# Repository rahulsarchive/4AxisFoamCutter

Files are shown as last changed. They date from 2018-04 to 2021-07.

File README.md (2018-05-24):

# 4AxisFoamCutter

Our goal was to build an UAV out of foam, since there will be many crashes involved, we decided to make a device to help us get through the iterations a bit faster. A hot wire cutter is the most efficient way to cut foam. A CNC hot wire cutter is even better! It is an awesome tool to have when you are building airplanes out of foam. A properlly configured machine can save you a lot of time and produce a smooth cut.

Mechanically, its not complicated to make a CNC Hot wire cutter. All you need is 4 independed linear axes, two horizontal axes and two vertical axes stacked on top of it. This can be acheived by any means such as linear bearings, smooth rods and also drawer slides. The axes are driven by stepper motors. There are minimal cutting forces involved, the machine only needs to be rigid enough to witstand the tension of the wire streched between the towers.

The problem is how to control 4 independent axes at the same time. Most tutorials online are for 3-axis 3D printers. Then there are documentation on people using expensive software and difficult to find hardware for making their 4-axis foam cutter.There does not seem to be enough documentation on building a 4-axis machine using easily available parts such as parts from a 3D printer kit and open source sotware. We found some people who had done similar projects using Arduino and Grbl, and decided to make a CNC hot wire cutter ourselves and try it out.

## Hot wire CNC Resources

[Hot wire cutter, RcKeith](http://www.rckeith.co.uk/cnc-hot-wire-foam-cutter/)  
[4-axis cnc hotwire cutter (arduino+Ramps)](https://www.rcgroups.com/forums/showthread.php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)  
[WingGcode](https://github.com/swarfer/winggcode)  
[Airfoil coordinates database](http://m-selig.ae.illinois.edu/ads/coord_database.html)  
[Free CNC Software](http://www.rckeith.co.uk/free-cnc-software-3-and-4-axis/)  
[4-axis Arduino based Hot wire cutter](https://www.rcgroups.com/forums/showthread.php?2388809-4-axis-Arduino-based-CNC-hot-wire-foam-cutter)  
[Devcnc Foam cutting software](http://www.devcad.com/eng/devcncfoam_f1_3.asp)  
[Jedicut foam cutting software](https://www.jedicut.com/)  
[Arduino Uno based foam cutter](https://sites.google.com/site/foamcuttercnc/software)  
[Nichrome wire Application Calculator](http://www.jacobs-online.biz/nichrome/NichromeCalc.html)  
[G-codes simply explained](https://all3dp.com/g-code-tutorial-3d-printer-gcode-commands/)

## Hardware

1. Plywood (12mm)
2. Rails (Steel tubes, Smooth rods)
3. Stepper Motors (one for each axis)
4. Lead screw (M8 x 600mm, as long as you need the axis to be)
5. Ramps 1.4
6. A4988 Stepper driver (one for each axis)
7. Arduino Mega 2560
8. Nichrome wire (30 guage for smaller builds and 26 guage for larger ones)
9. M8-M5 Motor coupler (M8 for the thread and M5 for the motor shaft)

## Software

1. Grbl Hotwire Controller   
2. 4-Axis G-code Generator  
    1. Wing Gcode  
    2. Jedicut  
    3. FoamXL  
 
We realized that the most difficult part of making a CNC hot wire cutter was the G-code and Controlling systems. So we decided to start from there. In our inital research we found many people using DevFoam and profilli for generating the G-code and using Mach3 to control their machine. But unfortunately, these softwares were not free and to run a Mach3 machine you need a parallel port, which is outdated now. Then our search lead to an Arduino based 4-axis cutter developed by [Marginally clever](https://www.marginallyclever.com/) which used an arduino Mega2560 and the Ramps 1.4 CNC sheild.

His page has codes for moving 4 independent axis and a Java based [G-code sender](https://github.com/MarginallyClever/GcodeSender) application that could send the the G-code secquentially to the Arduino using the serial port. We tried this solution and after some fiddiling around, we got it working. Not the easiest or most straight forward method. There is almost not documentation on how to use it.

[RcKeith](http://www.rckeith.co.uk/cnc-hot-wire-foam-cutter/) has some good documentation on the machines he built and what he used to control them. Some of them use expensive software and outdate hardware, which might be difficult to find.

We finally stumbled on a solution that worked, it was posted on a forum in rcgroups.com. Its for a [4 axis foam cutter using Arduino + Ramps1.4](https://www.rcgroups.com/forums/showthread.php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) It addressed the major problems we were having like a control software for the machine and generating 4-axis Gcode to drive the machine.

## Building the Machine

My intial design was based on Rckeith's foam cutter which used drawer slides as the linear guideways. This seemed like a good idea. They were locally available and rails are rigid without much backlash. The first design was for a machine with two towers on linear slides, with a total travel of the towers for about 20 inches. The machine would be laser cut out of 4mm plywood.

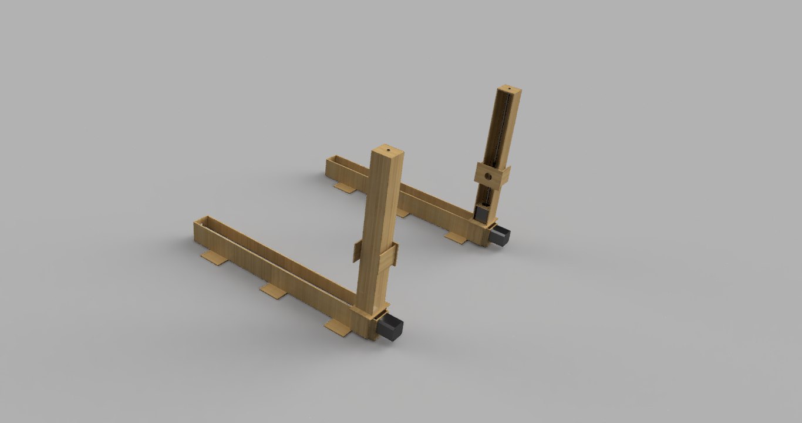
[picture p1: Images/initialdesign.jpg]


This was well and good, until we went to the shop to buy the slides. A 20 inch drawer slide can only travel 10 inches, so inorder to get 20 inches of travel we would need a slide of 40 inches, which were just too bulky and expensive for our use and the rails would protrude out of the machine for about 20 inches. Hence we dropped the plans for using drawer slides. Back to the drawing board.

We started on a new design for a more rigid maachine using smooth rods and leadscrews for motion.

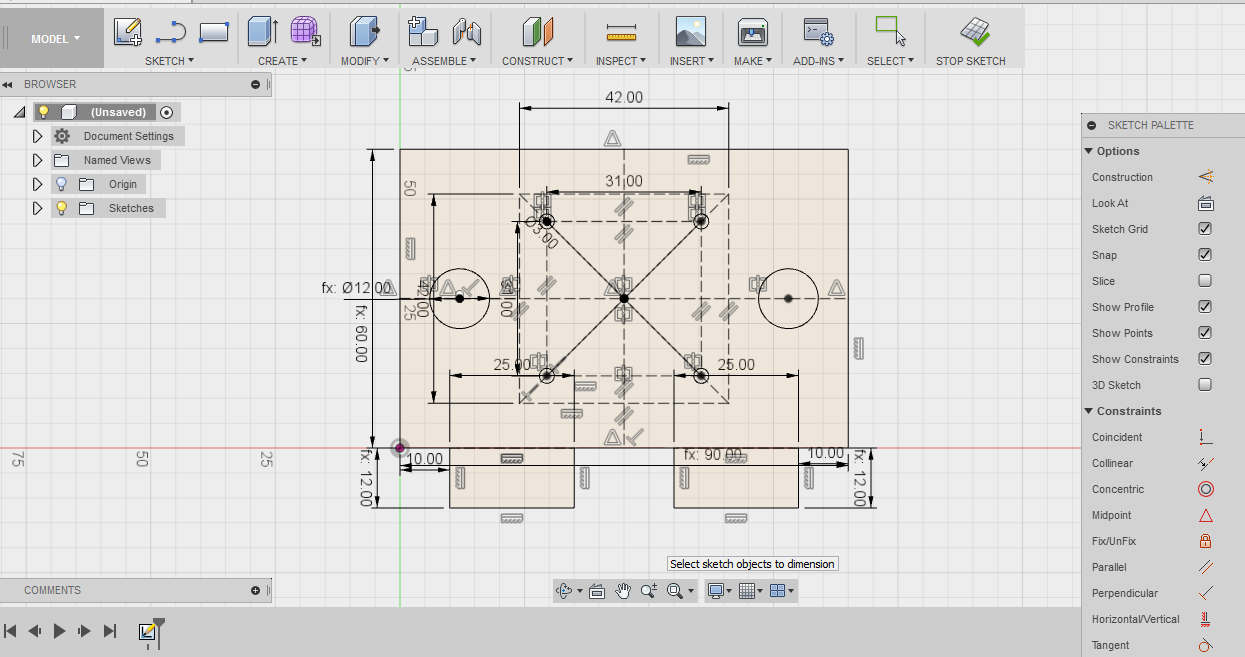
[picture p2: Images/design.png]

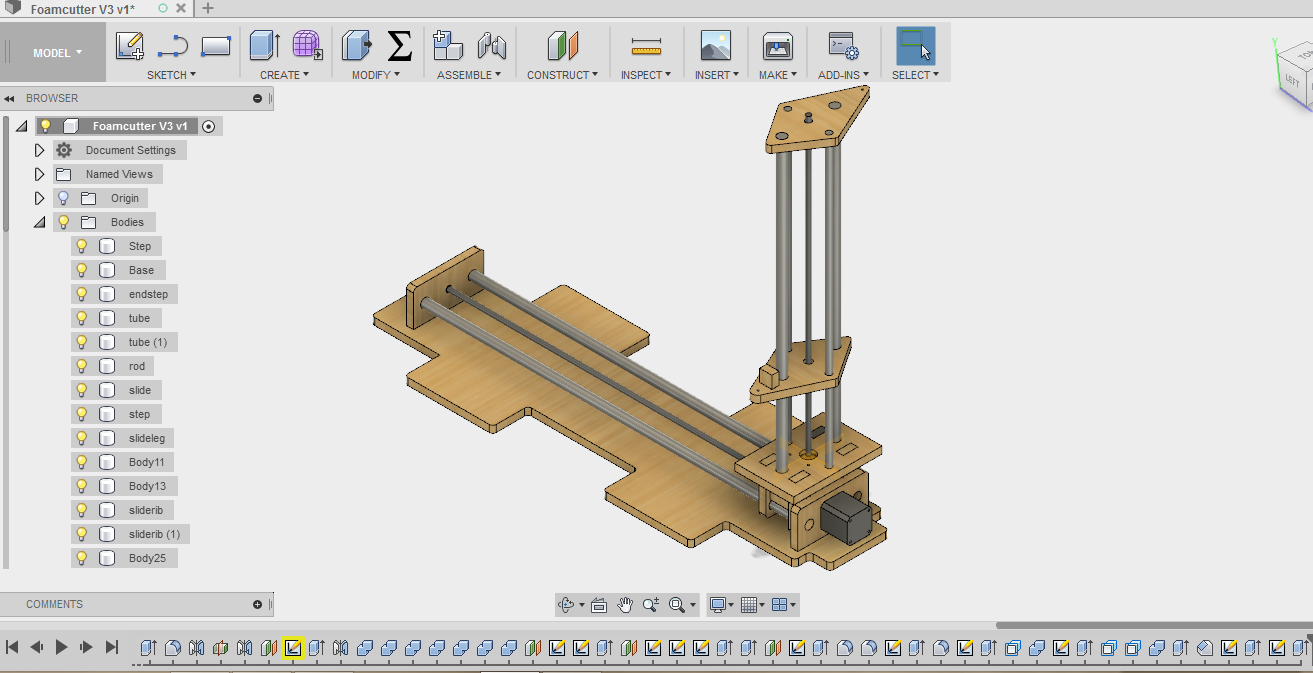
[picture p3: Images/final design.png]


The design is fully parametric. You can change the length of each axes, the diamter of the rods and even the clearance height of the vertical axis by changing the parameters in the file. On the vertical axes there are 4 rods to provide some torsional rigidity so the towers would not bend.

This is the fully redesigned machine using 1/2 inch steel tubes, 12 mm plywood as the base and M8 lead screws to move the axes. 

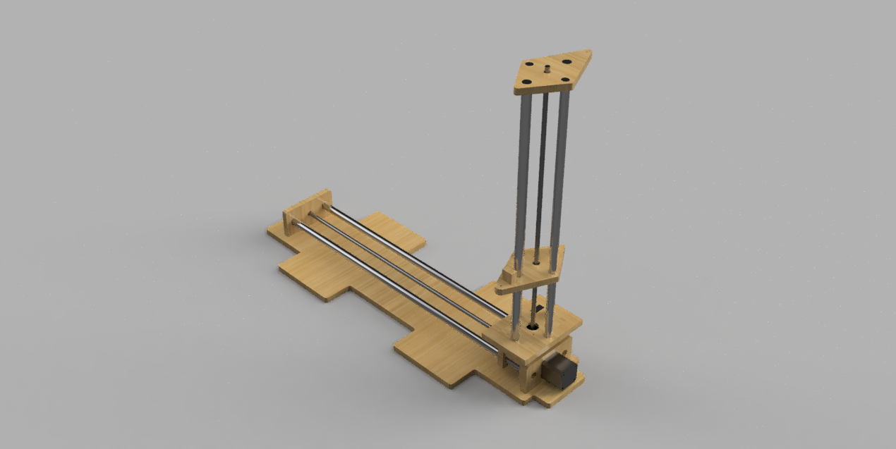
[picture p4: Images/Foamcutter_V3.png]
4 axis foam cutter


All the parts, except the lead screws were bought locally. The half inch steel tubes were not designed for linear bearings and there are not dimensionally accurate. So our plan was to 3D print a coupling for it to reduce the friction between wood and the steel.

The design made ready for milling on Shopbot (CNC mill) 

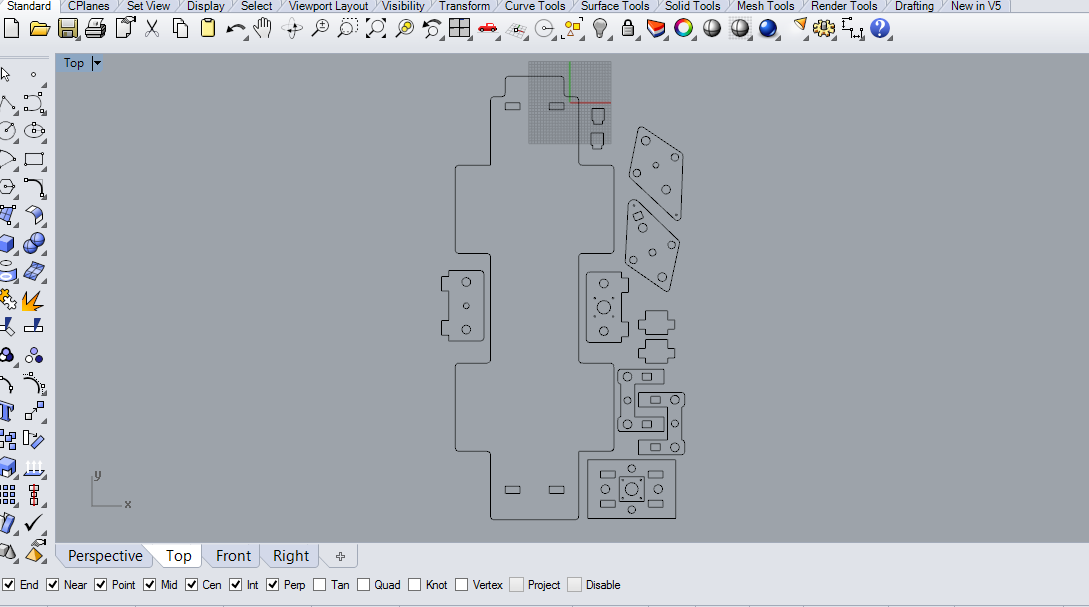
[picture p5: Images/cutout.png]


We cut the design by exporting the 2D DXF sketches and doing the CAM operations in Vcarvepro software. Since this is the intial version we decided to skip the couplers and go with wood on steel. we had to play with the tolerance between the circular hole and the steel tube to get it good enough to move on to the next step.

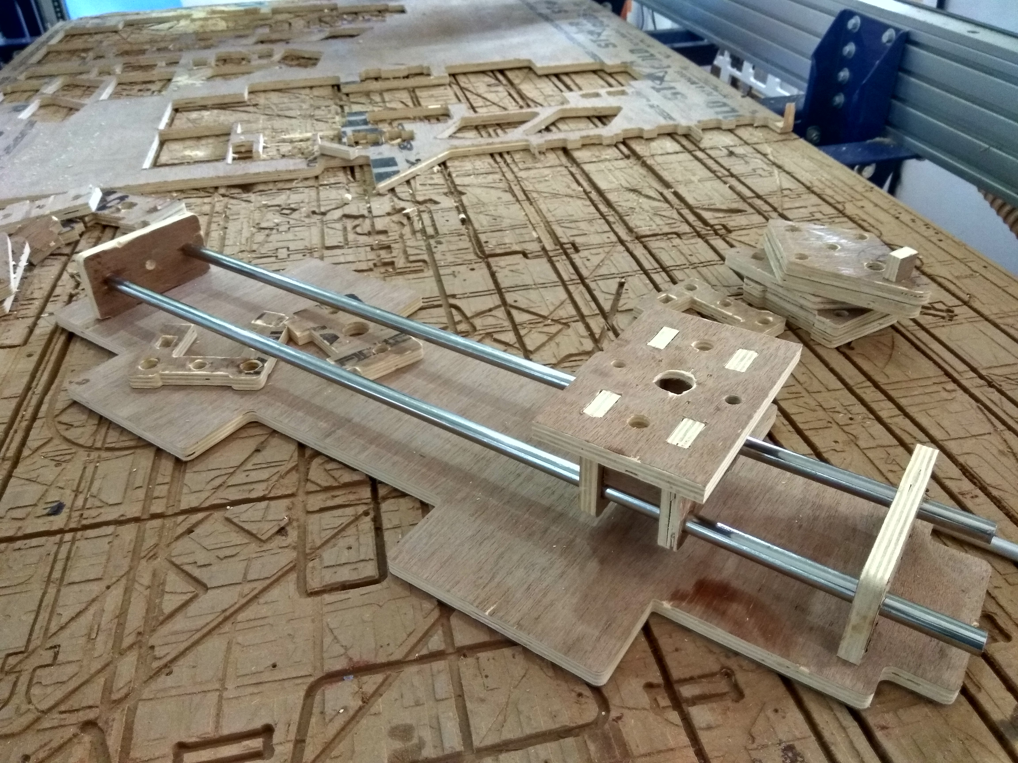
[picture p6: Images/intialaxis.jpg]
4 axis foam cutter


The first axis looks promising. The steel tubes are press fitted at the ends to form a rigid strucutre. The carriage is a bit loose but the motion is a lot smoother when a small amount of lubricant is applied. so we moved on to the vertical axis.

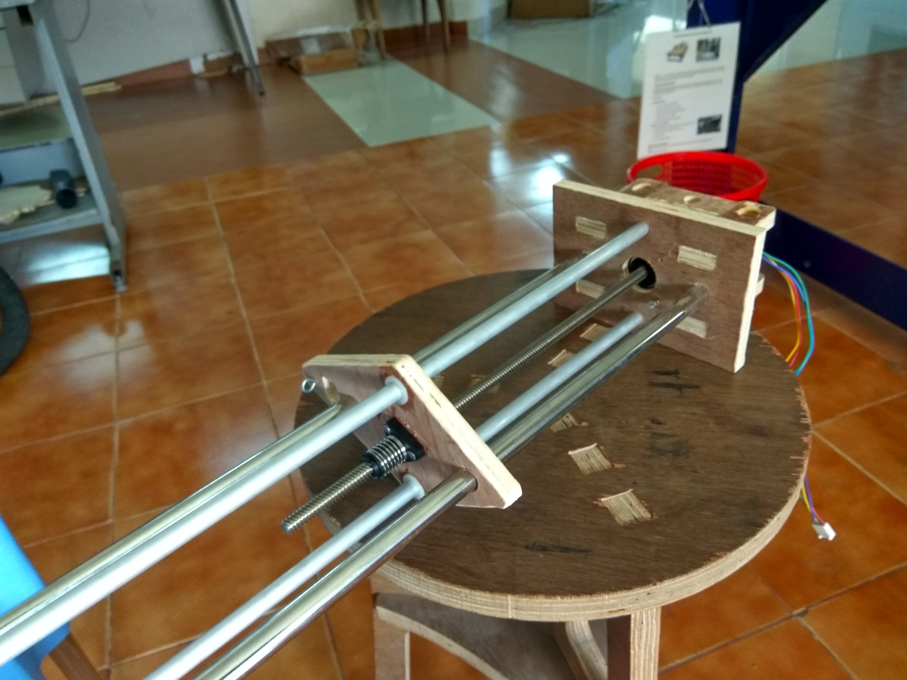
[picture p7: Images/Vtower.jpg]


The vertical axis has two steel tubes to carry the weight and two smaller aluminum tubes to provide tortional rigidity. We are using a stepper motor with an integrated lead screw to avoid using a coupler. 

The final assembled towers. All the rods are press-fit at the ends and loose fit on the steel rods to give a smoooth motion.

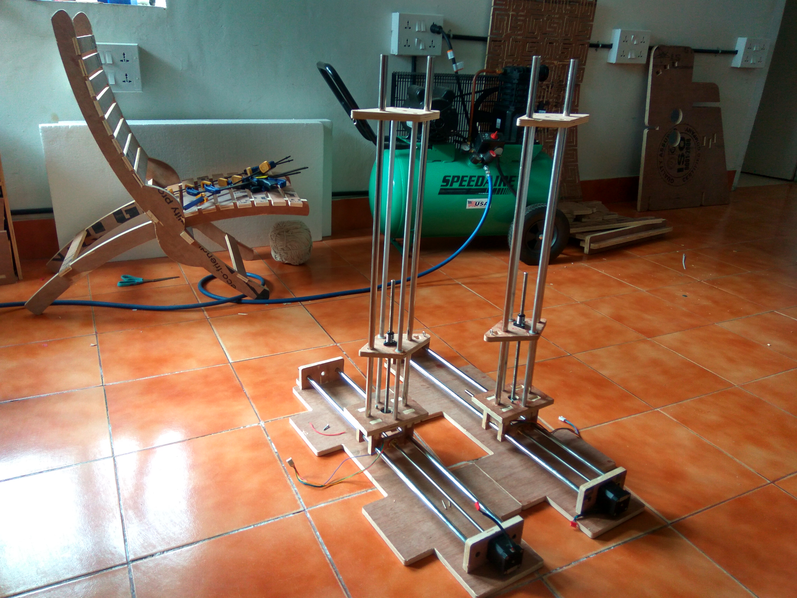
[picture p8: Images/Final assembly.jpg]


**Note-** When using sliding surfaces, depending on the material, a phenomenon called **'stick and slip'** can happen. This would cause the motion to become jagged and cause vibrations. It may also lead to surfaces locking up leading to excessive loads and missed steps when using a stepper motor.  

After the machine was assembled its time for fix the machine on a table, connect all the electronics and tie the Nichrome wire across the towers.

### Connecting the Electronics

We fixed the machine on a table using clamps. The base is designed to make it easier to use clamps to hold it in place. 

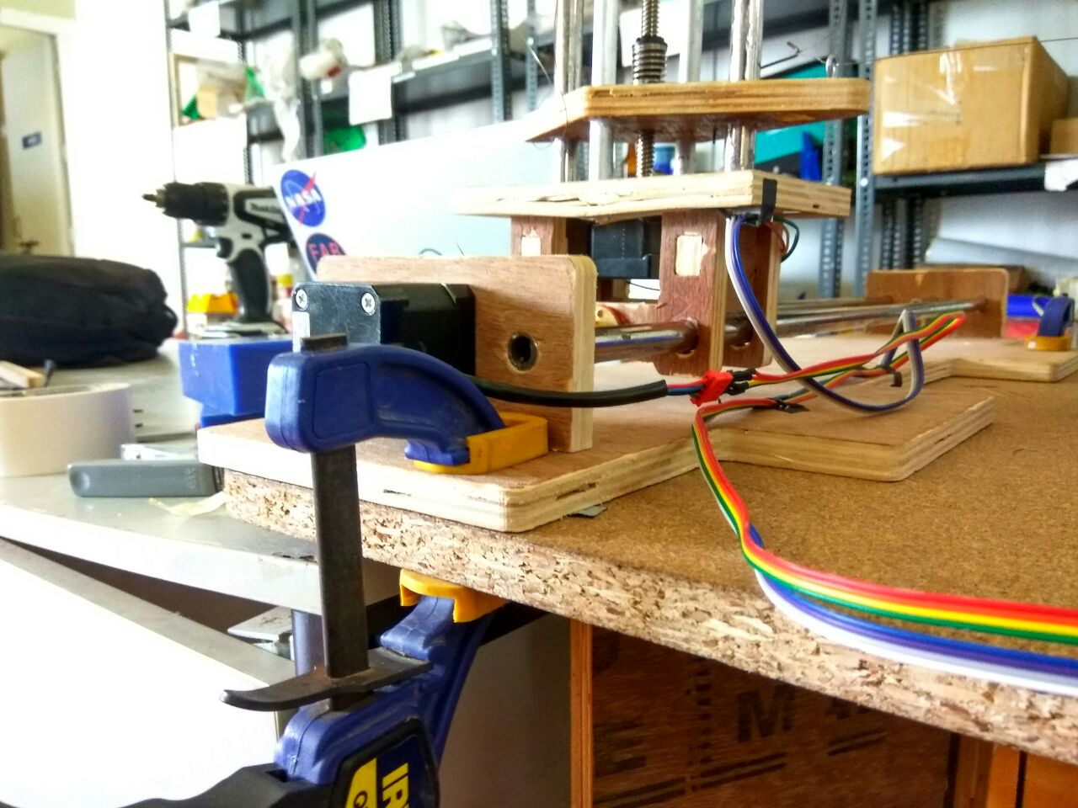
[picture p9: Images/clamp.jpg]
4 axis foam cutter assembly


The next step is to connect the electronics to move the motors and configure the machine. We have 4 stepper motors which need to be connected to our Ramps board. The wires need to extend enough to provide enough travel of the axes.

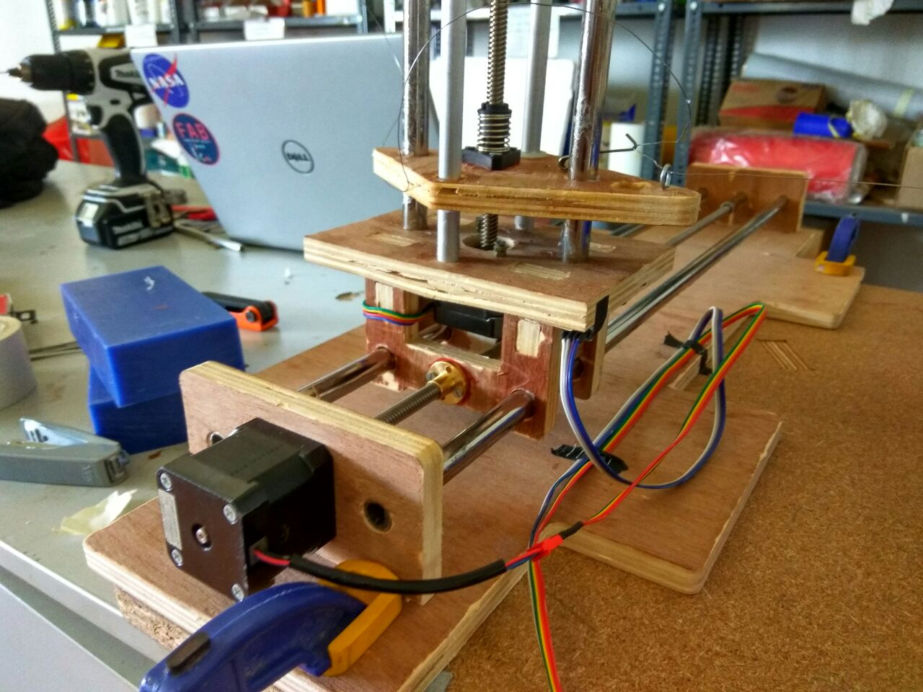
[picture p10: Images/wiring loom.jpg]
Wiring loom


All the wiring connects to our Ramps board, which is a CNC sheild for Arduino Mega2560. The Ramps can support upto 5 stepper motor drivers like the A4988. We are using Nema 17 motors with 200 steps per revolution running at 1/16th microstepping, giving us a smooth rotary motion.

The A4988 stepper drivers can be attached on top of the Ramps, one for each axis. Ensure **proper orientation** of the A4988 chip before attaching to the Ramps board. Each stepper can pull as much as 2 Amps, the stepper drivers have heat sinks to dissipate the heat. The board also has a 11A MOSFET on it to control the temperature of the wire connected to the D8 pin. All the components in the board will get hot, ensure proper cooling is provided. 

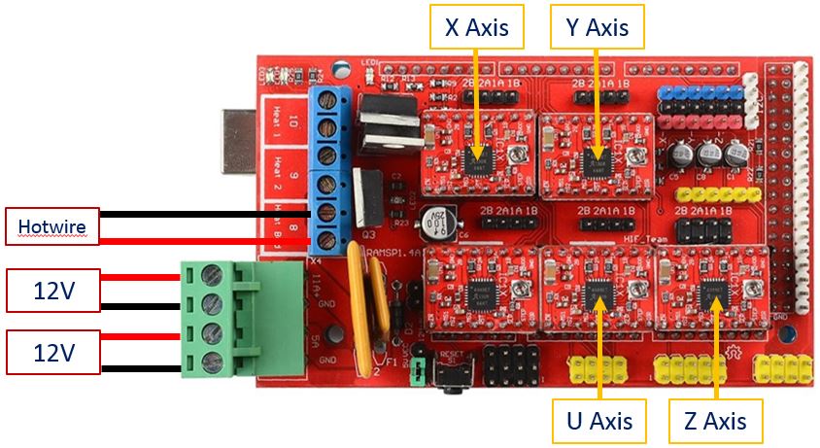
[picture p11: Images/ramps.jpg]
Ramps + Arduino Mega2560


**IMPORTANT**
When the system is powered on, the stepper motors continue to draw current to maintain the holding position. The components like Stepper drivers and Mosfets can get very hot during operation. Do not operate the Ramps board without **active cooling**.

In the begining we ran our machine without active cooling and lost 4 stepper drivers and bricked an Mega2560. After that we made a base for the board, attached it using spacers and put a fan to cool the board.

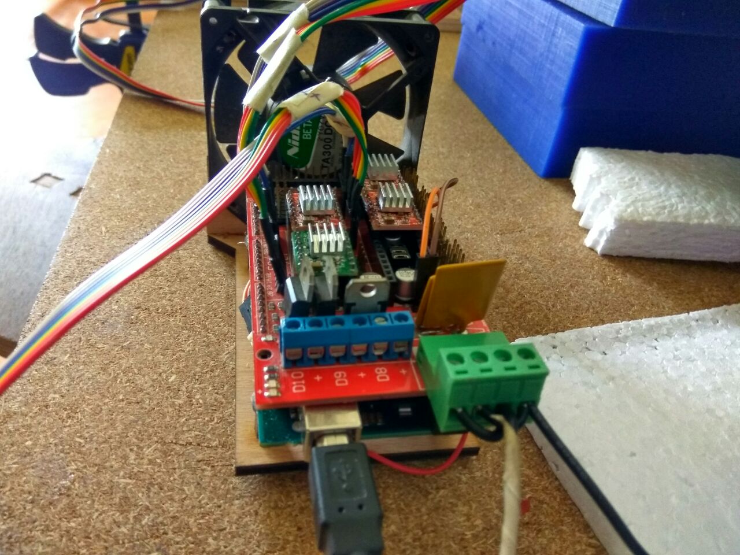
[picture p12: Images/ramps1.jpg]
Ramps + Arduino Mega2560


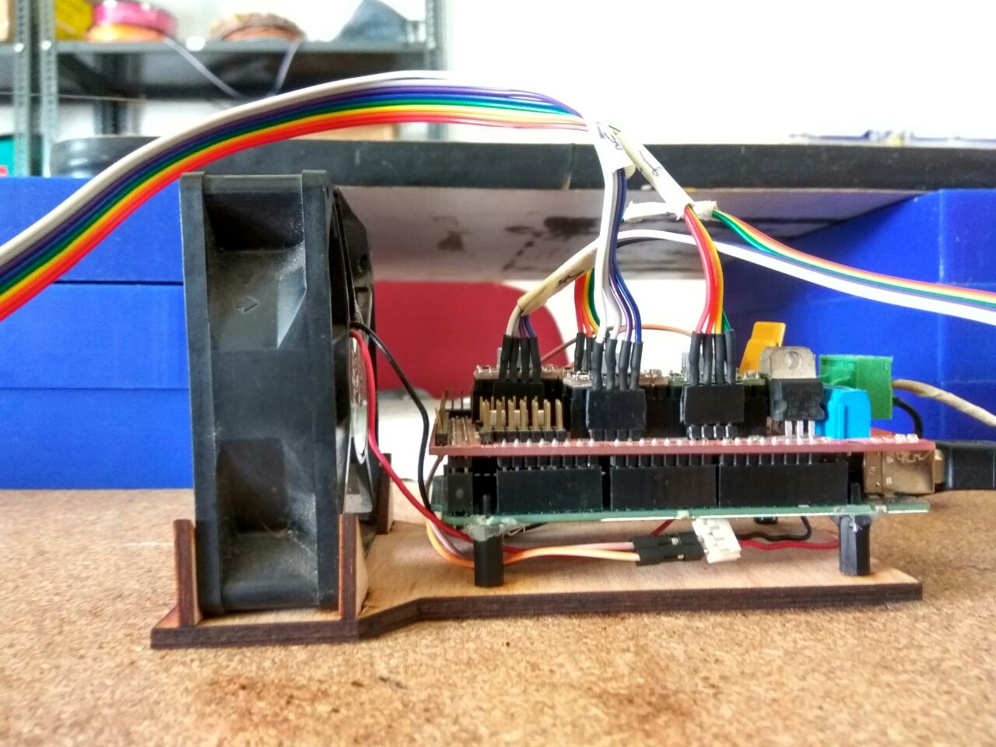
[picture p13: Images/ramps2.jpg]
Ramps + Arduino Mega2560


The board rests on spacers and is cooled by a 12V fan to prevent over heating of the board.

### Grbl Hotwire controller

We are using a Grbl control panel developed by [Garret Visser](http://github.com/Gerritv/Grbl-Panel/wiki) which was adapted for Hot wire cutting by Daniel Rascio.

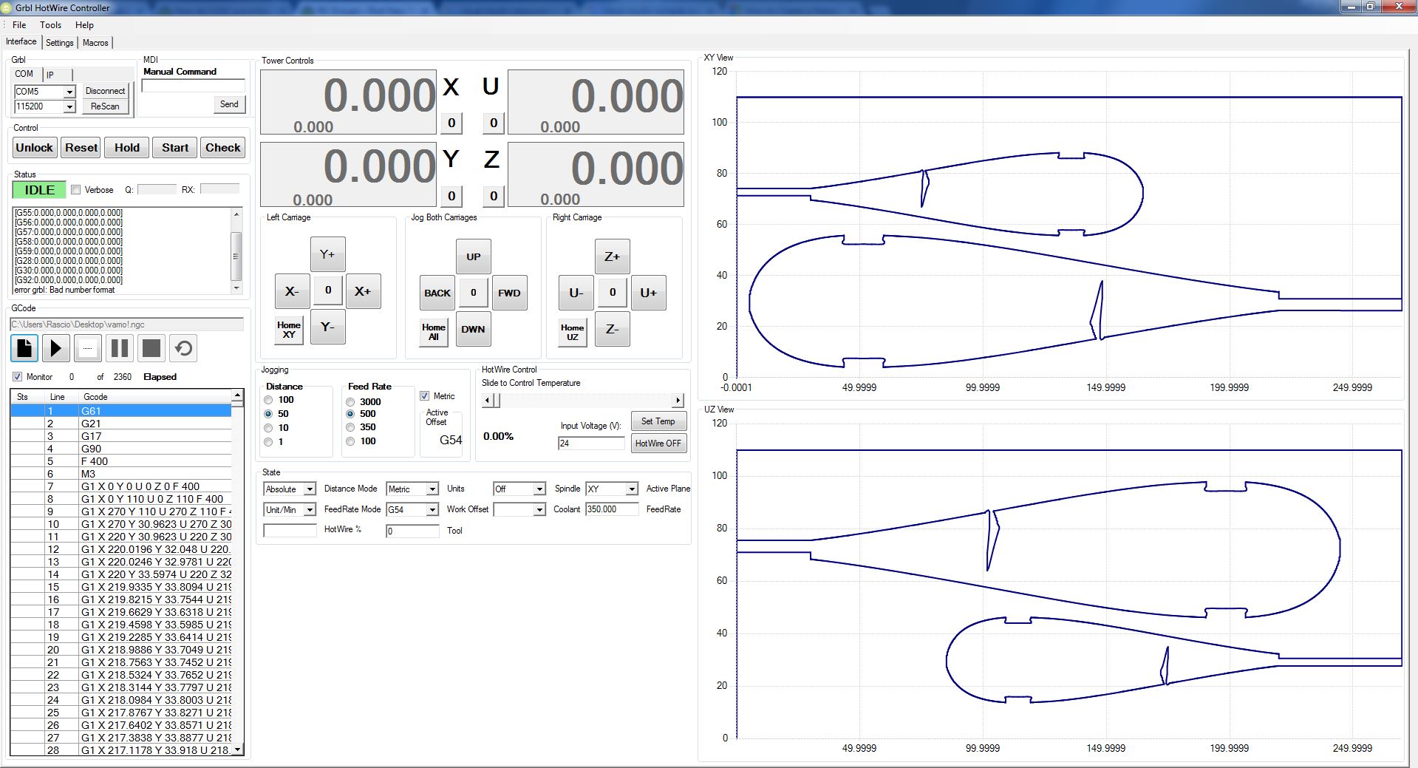
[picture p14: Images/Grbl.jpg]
Grbl control panel


The panel has Independent jogging control for all axis, including homing along with Gcode graph visualization, and the ability to save your own macros. The Hotwire temperature can be fully controlled using M3/M5 to turn ON/OFF and S"xxx" command to set the voltage output, either manually or via scroll bar in the software. The hotwire should be connected to "D8" output and is supplied by the power connected to the "11A" input on Ramps.

### Configuring the Machine

Every CNC needs to be properlly configured before operating. Since we are using stepper motors in an open loop system (without feedback) we need to know how far the carriage will move with every revolution of the Stepper motor. This depends on the **number of steps per revolution** of the motor, the **pitch of the lead screw** and the **level of microstepping** you are using.

 **steps_per_mm = (motor_steps_per_rev * driver_microstep) / thread_pitch**

After flashing the Megaa2560 with the Grbl8c2MegaRamps file, open the serial monitor and type '$$' to access the [Grbl settings](https://github.com/grbl/grbl/wiki/Configuring-Grbl-v0.9) panel. In order to change any value type the $number=value. Eg- $0=100
Once the machine is configured, ensure that the machine moves the exact amount as shown in the controller.

### Attaching the Hotwire

In order to cut foam using a hot wire you need a resistance wire made of a suitable material which can withstand the heat and will have a uniform temperature across the length.

Nichrome is a suitable material, I have seen some use steel fishing lines. This is a good article for [selecting a Nichrome wire](https://jacobs-online.biz/wire-xformer_selection.htm) for Hotwire cutting. Since our machine will use a wire length of more than 1 meter. we decided to use a 26 guage wire. It might be a bit too thick for our application. we will also test with a 32 guage wire and see how it goes.

The next step is to attach the nichrome wire to the machine, since we have 4 independent axis, we cannot just tie both ends of the wire to the towers. The wire needs to have some extension to it, either by means of a spring or a weight attached to the end.

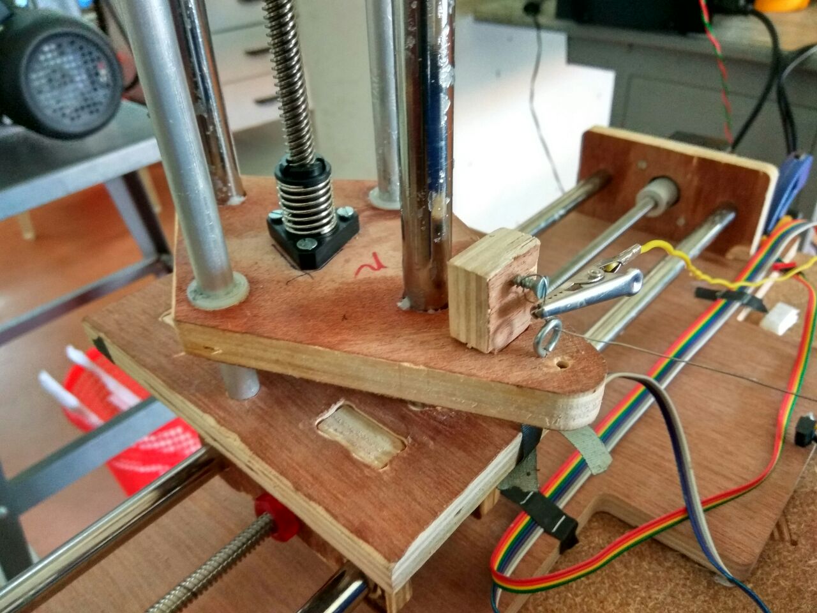
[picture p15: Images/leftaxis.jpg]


The hot wire is attached using hoops screws into the wood, these hoops help the wire move back and forth while maintaining the same height. A pulley would have been best, but we wanted to start with something simple and work our way up. In the left axis one end of the wire is attached to a screw, which is pulled up to maintain a level height at the hoop.

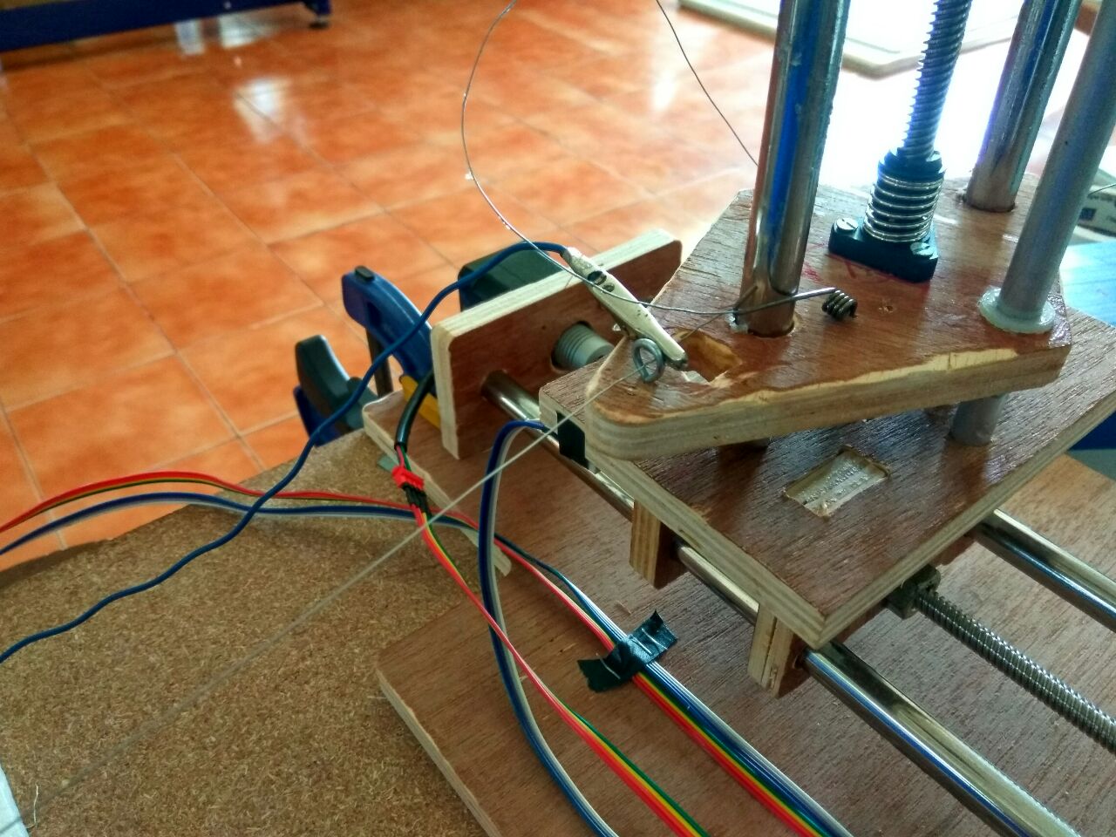
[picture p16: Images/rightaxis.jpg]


The other end of the wire is currently attached to the end of a torsion spring we had laying around, which will provide the necessary tension to keep the wire taught and to give some amount of flex so that the wire can extend and be pulled back.

### Generating the G-code

#### Wing G-code Generator

[Wing G-code Generator](https://github.com/swarfer/winggcode) is a program to generate XYUV G-code for hotwire cutting model airplan wings. It runs on python 2.7 and can also integrate with LinuxCNC's Axis interface. There is also an [online version](http://swarfer.co.za/rc/wire/index.php)

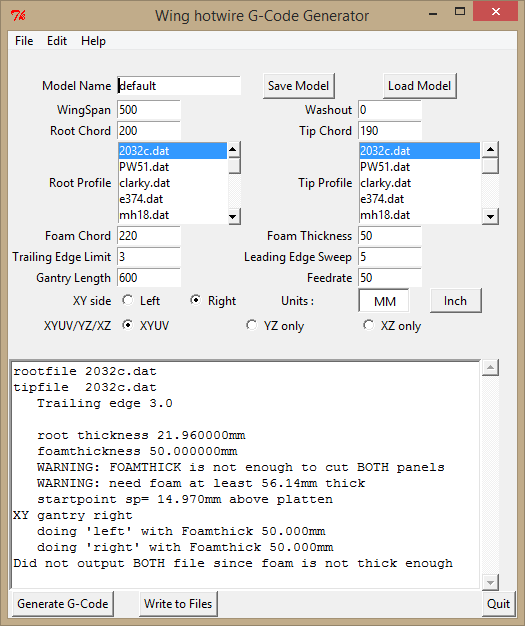
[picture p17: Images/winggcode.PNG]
Wing Gcode generator


It alows you to enter the parameters of the wing such as root chord, tip chord, Sweep, gantry length and even support washout. It has a database of airfoils in **.dat** format. New airfoils can be imported in the same way.

#### Jedicut 2.4

Jedicut is a cool piece of software in that it can do both CAD/CAM and also act as a machine controller. Thought the machine controller needs a PC with the old parallel port interface. But it also has a plugin to generate the G-code. It is not the easiest to configure. Some of the options and error messages are in french, but if you sit with it for sometime, you can get it working.

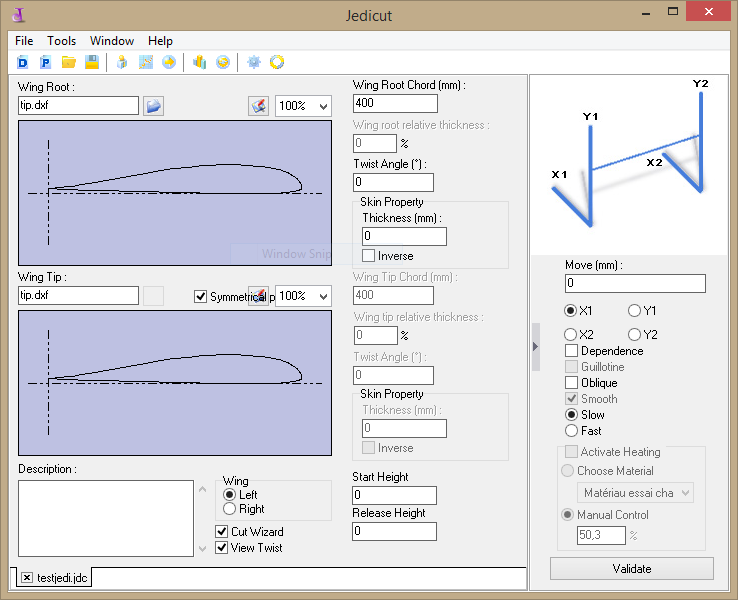
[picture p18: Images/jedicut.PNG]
Jedicut 4 axis g code


It has lots of features like cutting wizard to help you do sweept wings and compensate for wire kerf by adding a skin thickness. It can but more than wing profiles, it can cut out lettering and other shapes also.

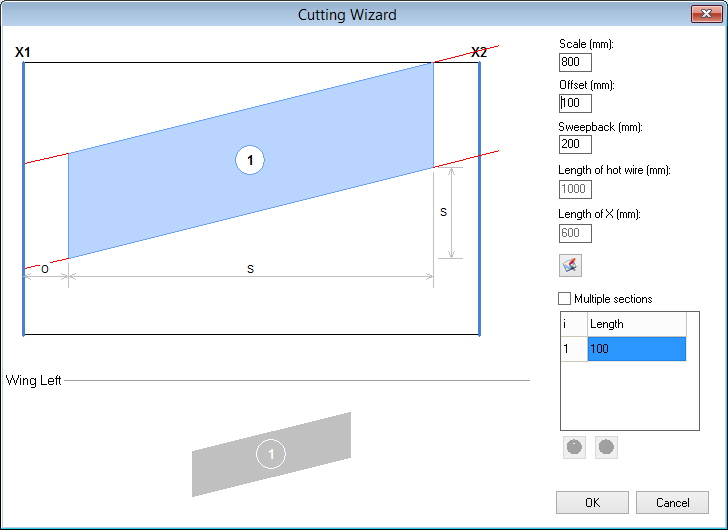
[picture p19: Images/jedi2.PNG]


***Note-**  Wing g-code generates G-codes in Absolute mode which works on Grbl without any issues, but Jedicut generates G-code in incremental mode. We had difficulty when first getting it to work, where the machine would just move back and forth. If this happens, Edit the G-code to remove unecceasry lines in the header.*

*Both Wing G-code and Jedicut generates G-code with some Grbl unsupported codes in the header, The controller will show in the monitor when such errors happen. Edit the G-code and remove unecessary lines of code.*

### Setting the Feed rate and temperature

Unlike conventional milling, the wire cuts by melting the plastic surrounding it, and when the tool stays in one position for some length of time, the surrounding material keeps melting away. This increases the kerf of the cut and cause dimensional inaccuracies. There are two variables which affect the kerf of the cut.

1. Cutting Feed rate.
2. Temperature of wire.

The **Cutting Feed rate** is the speed with which the wire cuts throuh the material. mostly denotes in **mm/sec**. The faster the speed the lesser the kerf, but the higher the temperature required and also tension in the wire has to be sufficent to withstand the cutting forces. Good starting speeds are around 350mm/s to 500mm/s.

The **Temperature** of the wire must be a bit higher than the melting point of the foam you are cutting. Ideally you want to cut with just the **radiant heat** where by the wire dose not acually touch the material but cuts in front of it. The temperature is governed by the amount of current which flows through the wire, which is determined by its voltage. There are softwares which allow for PWM control of the wire to heat is just right at the moments to optimize the cutting feedrate.

The temperature of the wire is determined by the square of the current times the resistance.

If you are using Nichrome wire,  

[Nichrome wire Application Calculator](http://www.jacobs-online.biz/nichrome/NichromeCalc.html)   

This is a cool application that can help you determine the temperature of the wire depnding on the lenght and the voltage applied. For our setup with a wire lenght of 850mm, we applied a voltage of **26V** and cut at a feed rate of **350mm/s**. This gave us good finish and very low kerf.

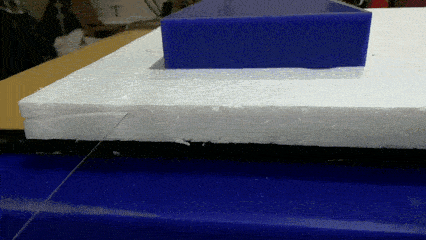
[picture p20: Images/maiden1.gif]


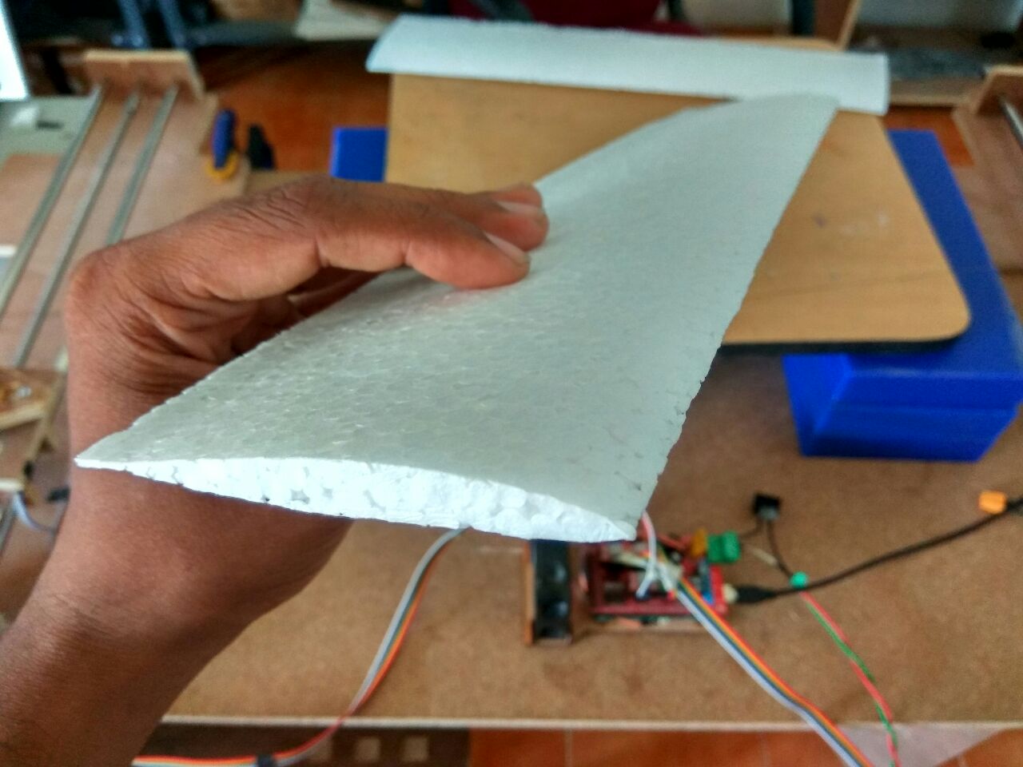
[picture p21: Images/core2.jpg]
cnc hot wire cut foam


### The Cutting process

The Process starts from the design, which is exported as a dxf and turned inot G-code by one of the softwares. The machine is turned on and calibrated, the material is placed on the workbench and the origin is now set. Turn on the hot-wire, run the G-code file and watch the machine do the work for you.

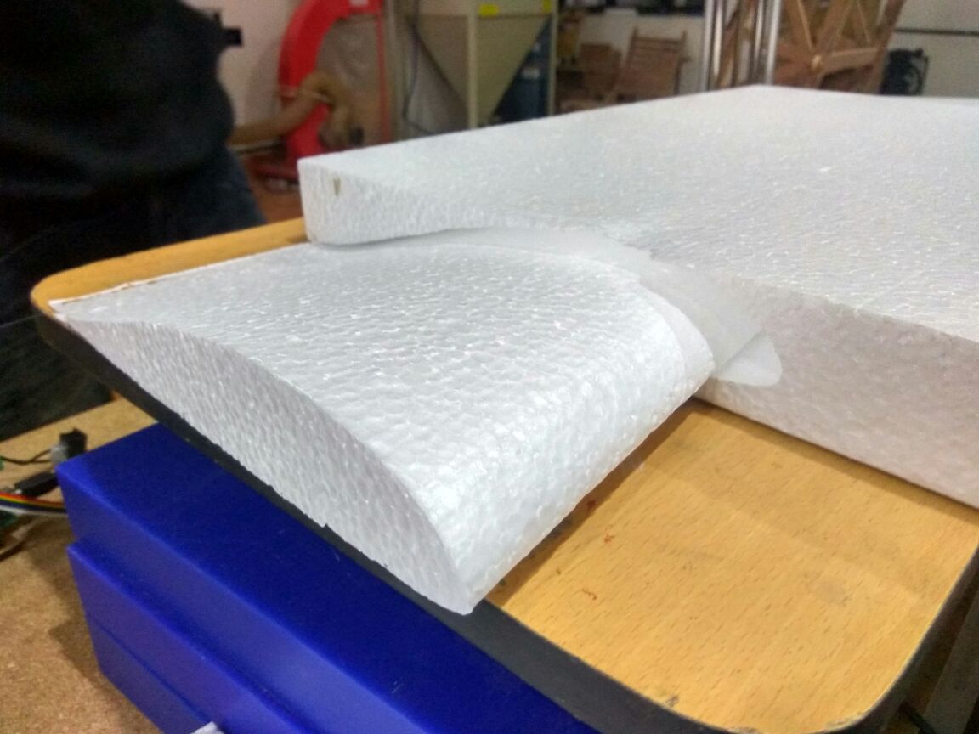
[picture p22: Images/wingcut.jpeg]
cnc hotwire 4axis foam wing cut



**Creative Commons — Attribution-NonCommercial-ShareAlike 4.0**

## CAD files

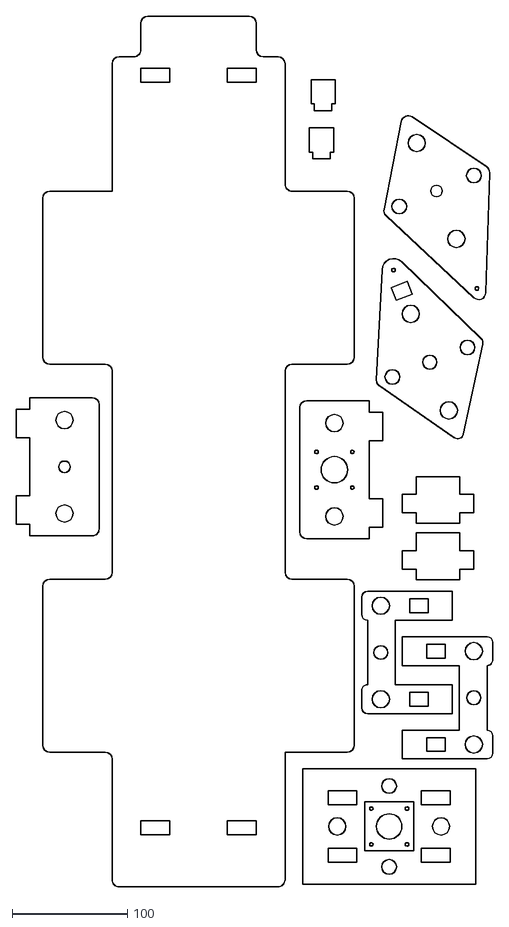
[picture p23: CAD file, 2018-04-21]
Design files/foamcutter12mm.dxf
413.6 x 755.0

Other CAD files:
Design files/foamcutter12mm.3dm

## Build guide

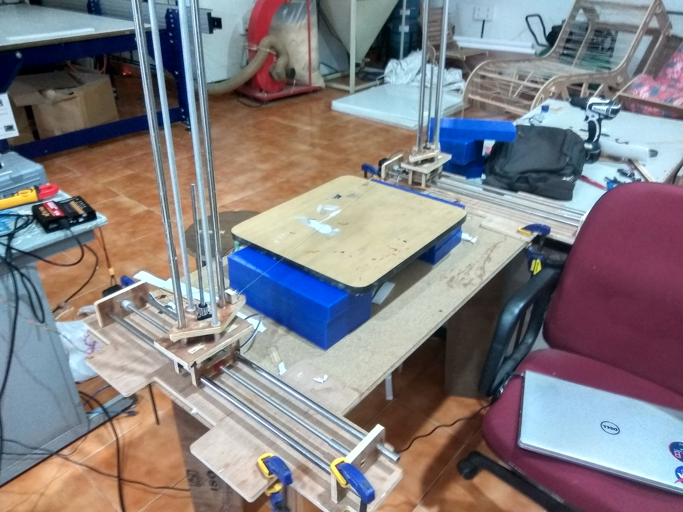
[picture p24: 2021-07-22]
Images/final setup.jpg

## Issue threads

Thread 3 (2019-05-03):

Damaged driver

cyberjunkiefr, 2019-05-03:
Hello,

First of all thanks for the great job this software worked from start without to much hassel.

My problem:
I don't use a arduino mega2560 board + Ramps v1.4 but a MKS BASE V1.6, wich is compatible with the Ramps1.4 and is a all in one solution (cheap).
Form start I just downloaded the sketch loaded it to my board and it was done!!

By  stupid mistake I damaged one of the oneboard drivers.
I hook the motors up like explained here.
X = E0
Y = E1
U (t-axis) = Y
Z = Z
I broke the u-axis (y) driver, but I still got the original driver for X-Axis not used.
I've been trying to understand, wich pins to set up to "connect" the u-axis to the physical x-axis.
I found this in pin_Map.H
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

Now I'm trying to understand the pinout of the mega2560 board (shield connector) and the corresponding pinout of the ramps1.4 board.
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

That's where I'm lost.
Can somebody tell me what value I should use for #define T_STEP_BIT and
#define T_DIRECTION_BIT? so that the T-AXIS would be connected to the physical X-AXIS driver.

And meaby some explaination about these values so I can understand better.
I want to hook up some 3-wire endstops to my machine so if I can figure it out my self I feel happy.

Thanks in advance

Roel Jaspers

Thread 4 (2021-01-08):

Where are the source code ?

Fjolnirr, 2021-01-08:
I cant find the arduino program can you give me a link ?

rcKeith, 2021-01-08:
I have the later firmware pre-compiled which you can use Xloader to install and an updated windows application. With full configuration details.  https://rckeith.co.uk/file-downloads/  and https://rckeith.co.uk/grbl-hotwire-mega-5x-for-cnc-foam-cutters/

Full tutorials on YouTube as well

rcKeith

Closed 2021-02-22.

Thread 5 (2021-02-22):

Soft Limit Switch (#20) is not working.

Fjolnirr, 2021-02-22:
I have followed rckeith tutorial https://www.youtube.com/watch?v=T2yhzRf1N0w for endswitches. My machine works perfectly(only tried manual controls not g-code yet). My switches also works when pressed( becomes ticked) however while #20 set to 1(soft switch) when press any move button(x,y,u,z) it does not move and pops an error about JITdebugging i guess. and after that when i click continue for example x+ moves but does not change the distance of x and does not go backward after a certain distance. And sometimes nothing moves not even 1 direction. Anything to help me ?

rcKeith, 2021-02-22:
Download the latest version from [here](https://rckeith.co.uk/download/grbl-hotwire-mega-5x-application-v-4-00/) . It shows standard GRBL error messages which should help identify the issue.
keith

Fjolnirr, 2021-02-23:
Hey thanks for your answer i have upgraded to the latest. Now the errors is clear here my settings and error message i get:
Start up gives an Alarm
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
Error message i got when soft switch is 1
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
My settings
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

rcKeith, 2021-02-23:
Hi
Have you installed end-stops/limit switches?
Soft limits can be a little confusing. It means you have 4 end-stops
installed for the XYUZ min and then $130-131 is used to set the max travel.

Keith

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

Fjolnirr, 2021-02-23:
Yes i have installed end-stops, 4 of them working verywell. I can observe their condition in limit switch status section.

rcKeith, 2021-02-23:
From your screenshot it looks like you are trying to jog before you have
homed the machine. The red Homing button will go off once you have homed.
Just click on it to home and then jogging should be fine.
Keith

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

Fjolnirr, 2021-02-24:
I have tried to home. But it tried to run through switch. And this error poped.
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

Fjolnirr, 2021-02-24:
I have discovered something. I have push the switches when machine homing. However U,Z,Y starts homing with + direction and goes away from switch first and i push the button when it goes away it pulls-off and then i click one more time and they are set. Bu this is wrong cause X goes to - direction and it sets the x homing.

You might think that my motor directions are wrong however they are correct. Cause manually when click x,y,z,u at + direction it goes away from switch. It is probably some dir settings but i dont know which one? can you direct me to that setting?

rcKeith, 2021-02-24:
Hi
The problem is the homing invert mask which you need to set to make the X
home in the other direction. Looking at your setting try changing $23=0
looks like you have it set to 1.
If not you will need to try other values  Check my web page where all the
setting are explained
https://rckeith.co.uk/grbl-hotwire-mega-5x-for-cnc-foam-cutters/

Keith

<http://www.rckeith.co.uk>
http://www.rckeith.co.uk

On Wed, 24 Feb 2021 at 10:34, Yusuf Can Anar <notifications@github.com>
wrote:

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

Fjolnirr, 2021-02-24:
Thank you. Issue is solved. I am closing this.

Closed 2021-02-24.

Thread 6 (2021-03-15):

Hot wire

Fjolnirr, 2021-03-15:
Hi Keith,

I have build the machine using your video with arduino mega2560, ramps board. I am also using grbl5. Unfortunately my hotwire does not get hot. I am setting temp 12V in the software output from d8 which is perfectly works i can read the 12v output with multimeter.

Here is my wire specs:
90 cm length,
30 GA( 0.25 mm diameter) nichrome
27 ohms measured for the given length and diameter

With this specs (12 = 27. I) I get 0.44 amps which is not even warming the wire. Can you tell me how much current do i need ?

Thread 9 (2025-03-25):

Excellent project, is the adapted gcode sender available anywhere?

concretedog, 2025-03-25:
Hi, fabulous project. I'm thinking about building my own but am wondering if the adaption of the gcode sender you diud is available anywhere? I see the link to the original sender it's based on, or are the modification you did to that sender documented anywhere? Thanks.

concretedog, 2025-03-25:
Ah sorry I've realised it's the GRBL Hot wire controller you are using and have found it.

Closed 2025-03-25.

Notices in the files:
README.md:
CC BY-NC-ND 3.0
